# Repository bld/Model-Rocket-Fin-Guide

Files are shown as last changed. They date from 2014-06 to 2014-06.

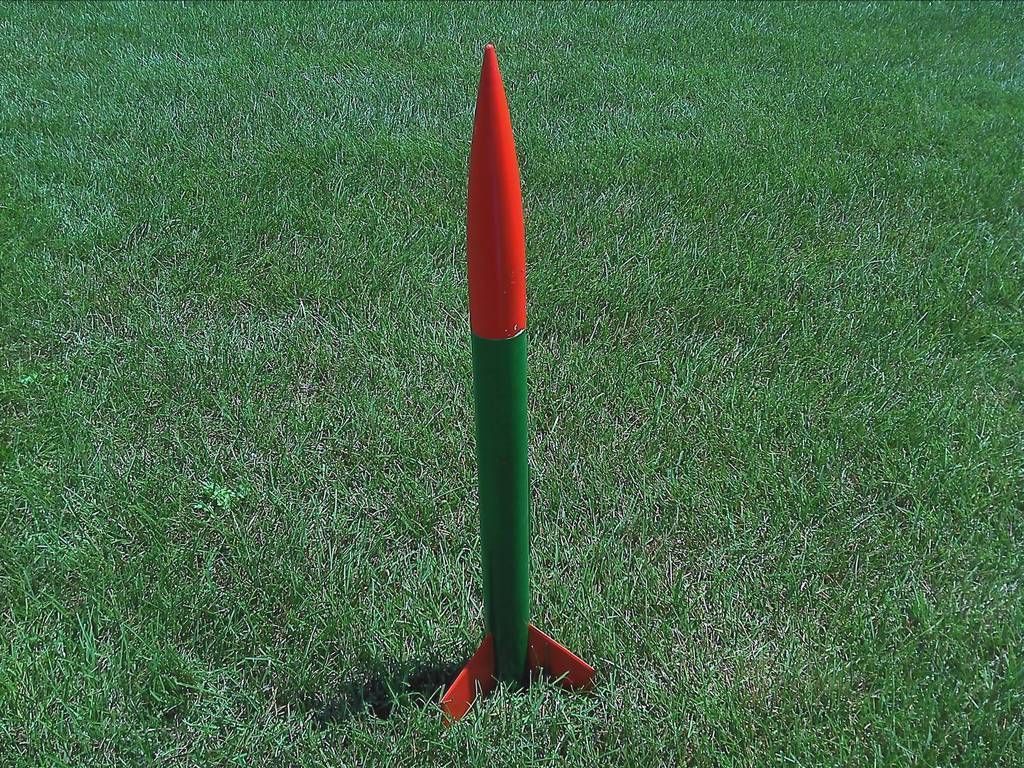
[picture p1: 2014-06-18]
Completed_rocket.jpg

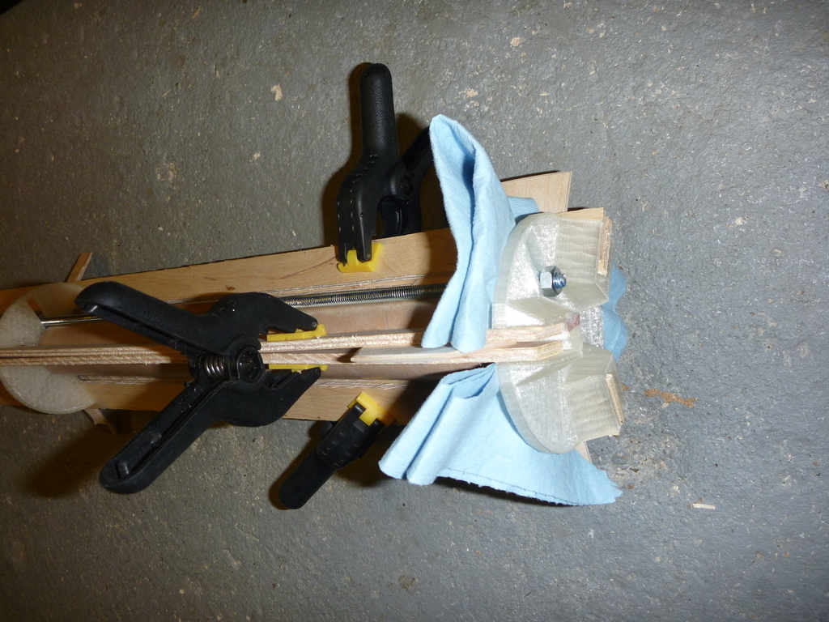
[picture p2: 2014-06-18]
Jig_clamping_fins.jpg

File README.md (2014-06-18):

Model-Rocket-Fin-Guide
======================

I was building my first high powered rocket - a LOC Precision Aura -
and I wanted a jig to epoxy the fins and launch lug on straight. I
designed this thing to print a pair of jigs to stick in either end of
the body tube - one end with engine mount. The fins are held with
strips of thin plywood held with spring clamps & wedges. A piece of
threaded rod with nuts on either end holds the launch lug in place,
while putting the jigs in tension. This setup allowed me to epoxy all
the fins and the launch lug at once.

Licensed under [CC BY-SA 3.0](http://creativecommons.org/licenses/by-sa/3.0/).

Instructions
------------

Materials required
* 2 plates
* 2 adapters (body tube and/or engine mount)
* Threaded rod or other long, thin rod or stick to hold launch lug. Longer than body tube.
* 6 thin plywood strips to clamp fins (longer than body tube, ~1" or 3/4" wide, ~1/8" thick)
* 3 (or 6) small plywood strips (~1/2" x 2") thicker than fin material for use as wedges.
* 3 spring clamps
* Epoxy (or glue for lower power rockets)
* Paper towel to catch dripping epoxy

1. Take measurements and modify parameters in .SCAD file.
   * Inner diameter of body tube, and engine mount if applicable
   * Thickness of fin material
   * Thickness of plywood strips to clamp fins
   * Rod diameter - leave some clearance
   * Inner body tube diameter - leave ~0.5mm clearance
   * Engine mount inner diameter - leave ~0.5mm clearance
   * For very large body tubes, check to see if your printer is big enough - my Mosaic was big enough to do a 100mm diameter plate - plenty big for my 38mm diameter rocket.
   * Check other parameters to make sure they work for your situation.
2. Print 2 plates. I provided an STL for my situation.
3. Print 2 adapters - one to fit each end of the body tube, which may have an engine mount in one end. I provided adapter STL files for a 38mm body tube and 29mm motor mount.
4. Check fit of adapters into body tube and engine mount - I had to reprint one, and reduce the others with a file.
5. Attach the adapters to the plates with an M3 cap screw and nut. I put the paper towel in between the adapter and bottom plate to catch epoxy, cutting slots for the fins and rod to hold the launch lug.
6. My body tube was pre-marked with lines for the lug and fins. You can mark a straight line by laying the body tube next to a straight piece of wood on a flat surface and using it as a ruler.
7. Put threaded rod through the enclosed slot on one jig. Slip launch lug over it. Put rod through other slot. Put nuts on either end. Make sure one end is inside the fin slot blisters so it can stand on that end. Align with line marked on tube. Tighten nuts.
8. Put a pair of plywood strips in each set of slots. Put fin between the strips up on body tube where there is room. Slide fins down until they reach the location along the body tube desired. In my case, the fins stuck into the bottom jig slots. If you want the fins up higher, you may need a 2nd set of plywood wedges.
9. Attach spring clamps to the plywood strips just above the fins to hold them.
10. You may notice a slight gap between the fins and body tube. I fixed this by pulling the upper end of the plywood strips away from the body tube until they are part of the way out from the body tube. Then, stuff the plywood wedges in between the strips above the jig until the strips are firmly held in the upper slots. Now, push the top of the strips into the slots. This will push the fins firmly against the body tube.
11. Now that you know where everything goes, pull the strips a little ways out from the top of the body tube, apply epoxy between the base of the fins and body tube, and push them back against the body tube. Loosen one nut on the rod holding the launch lug and apply epoxy at the correct position. Mine was ~half way up the tube. Press rod against the body tube at top and bottom and tighten nuts.
12. Now that the fins and launch lug are firmly secured, you may be able to stand the whole assembly upright. If not, find a way to support it vertically so that if the epoxy runs, it runs down symmetrically.
13. Once the epoxy is dry, apply thickened epoxy fillets to the base of the fins and launch lug. Allow to dry.

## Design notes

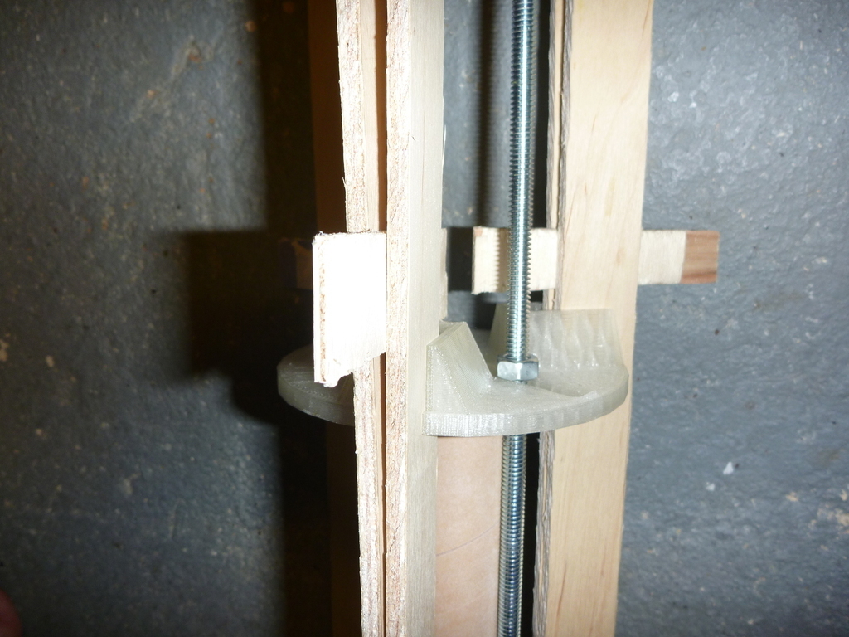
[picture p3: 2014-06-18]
Closeup_of_wedges.jpg

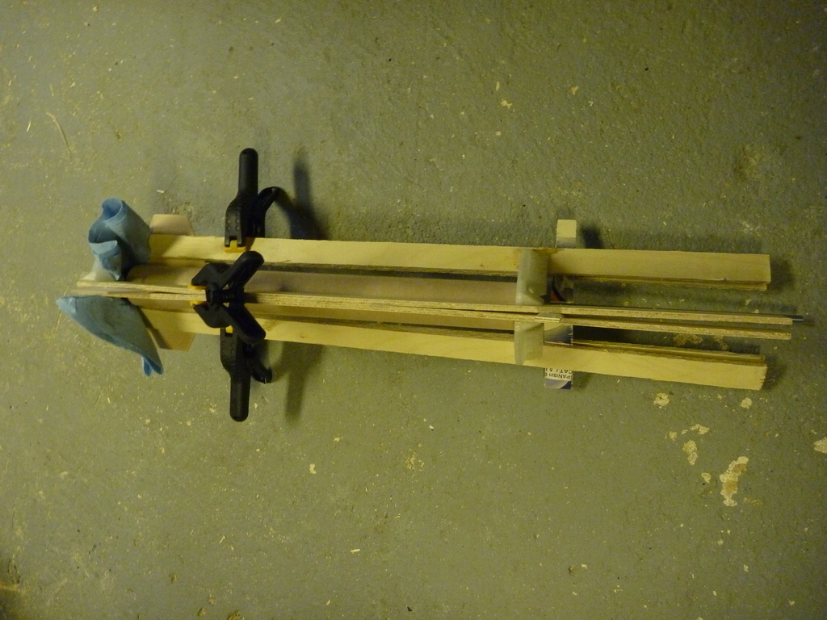
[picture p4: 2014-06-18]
Jig_in_use.jpg

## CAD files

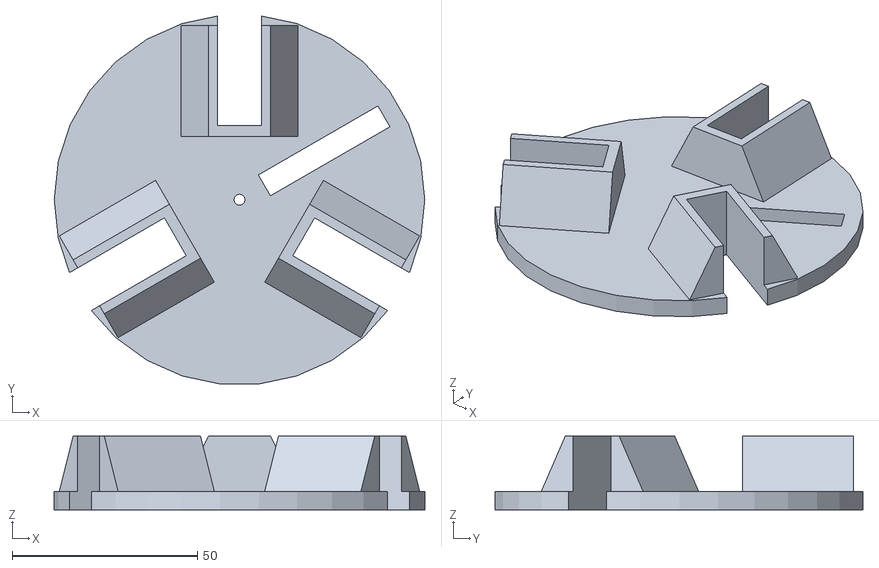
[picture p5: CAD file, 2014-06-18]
plate.stl
100.0 x 99.3 x 19.9

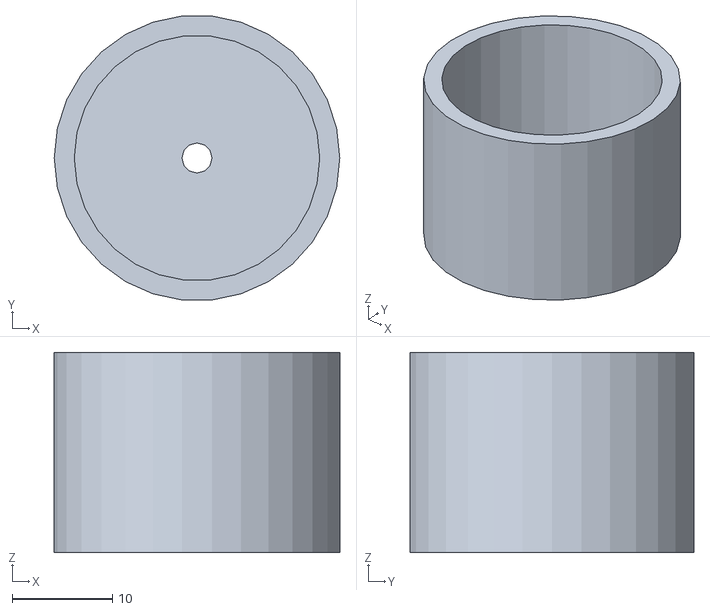
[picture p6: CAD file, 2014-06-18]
adapter28.5.stl
28.5 x 28.3 x 20.0

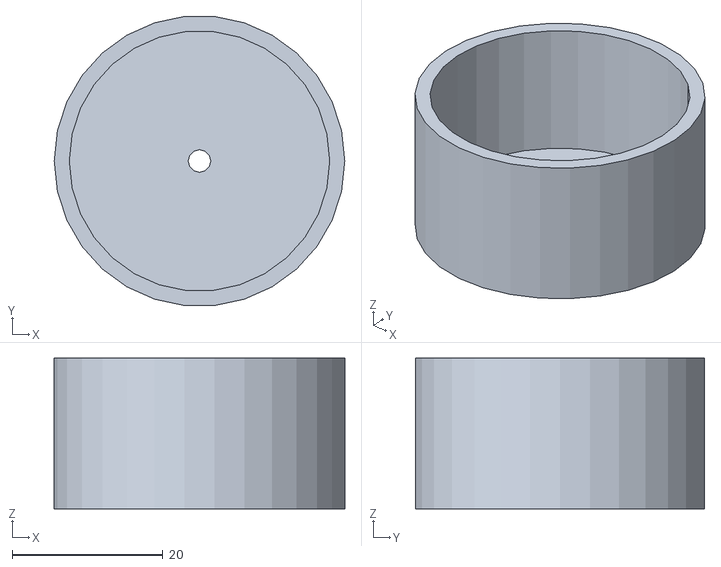
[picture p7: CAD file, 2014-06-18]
adapter38.5.stl
38.5 x 38.3 x 20.0

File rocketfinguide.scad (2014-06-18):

// Rocket fin guide
// Print 2 plates and 2 adapters that fit in the body tube / engine mount

plateod=100; // plate outer diameter - 100mm to fit on my Mosaic
plateh=5; // plate height
nfins=3; // number of fins
fint=2.8; // fin thickness
stript=4.5; // thickness of strips used to clamp fins
screwd=3; // diameter of screw to attach tube adapter (M3)
screwheadd=5.5; // screw head diameter (M3)
rodslotw=6.5; // width of slot for rod (fits 1/4" threaded rod)
rodslotoffset=5; // Offset of rod slot from outer edge and central screw hole
finslotl=30; // Length of fin slot
finslotw=fint+2*stript; // Width of fin slot - calculated from fin thickness & strip thickness

// Fin slot blister parameters
finsloth=15; // Height of fin slot blister
finslotbasew=20+finslotw; // Width of fin slot blister base
finslottopw=5+finslotw; // Width of top of fin slot bister
finslotoffset=3; // Displacement of fin slot blister in from outer edge


//tubeid=38; // Body tube inner diameter (for 38mm body tube)
tubeid=28.5; // Body tube inner diameter (for 29mm engine mount)
adapterh=20; // Height of body tube adapter
adaptert=2; // Adapter thickness

// Body tube / engine mount adapter
module adapter()
	difference(){
		cylinder(r=tubeid/2,h=adapterh);
		translate([0,0,adaptert]) cylinder(r=tubeid/2-adaptert,h=adapterh);
		translate([0,0,-1]) cylinder(r=screwd/2,h=adaptert+2,$fn=12);
	}


module finslotblister()
translate([0,plateod/2-finslotoffset,0])
rotate([90,0,0])
linear_extrude(height=finslotl)
	polygon([
		[-finslotbasew/2,0],[finslotbasew/2,0],
		[finslottopw/2,finsloth],
		[-finslottopw/2,finsloth]]);

module plate()
difference(){
	union(){
		// Plate
		cylinder(r=plateod/2,h=plateh);
		// Blisters for fin slots
		for(i=[0:nfins-1])
			rotate([0,0,i*360/nfins])
				translate([0,0,plateh-.1]) finslotblister();
	}
	// Screw hole for body tube adapter
	translate([0,0,-1]) cylinder(r=screwd/2,h=plateh+2,$fn=12);
	for(i=[0:nfins-1])
		rotate([0,0,i*(360/nfins)-30]) translate([plateod/2-finslotl,-finslotw/2,-1]) cube([2*finslotl,finslotw,plateh+finsloth+2]);
	rotate([0,0,360/nfins/2-30]) translate([screwheadd/2+rodslotoffset,-rodslotw/2,-1]) cube([plateod/2-screwheadd/2-2*rodslotoffset,rodslotw,plateh+2]);
}

plate();
//adapter();
